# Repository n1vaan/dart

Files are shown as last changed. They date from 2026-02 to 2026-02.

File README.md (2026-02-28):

# DART - A custom 12-DOF Quadruped Robot
This is a smart quadruped robot dog that imitates the Boston Dynamics robot Spot. It uses inverse kinematics logic, along with visual input through cameras and quantitive measurements through an IMU to inform it's walking and movement algorithmns.

### Why we made it

We set out to build a quadruped robot to better understand how complex systems like locomotion, balance, and perception work together in robotics. This project gave us the opportunity to apply concepts like inverse kinematics, sensor integration, and real-time control in a hands-on way. Building a walking robot also pushed us to think carefully about both mechanical design and software logic.

## Fully Assembled Prototype 
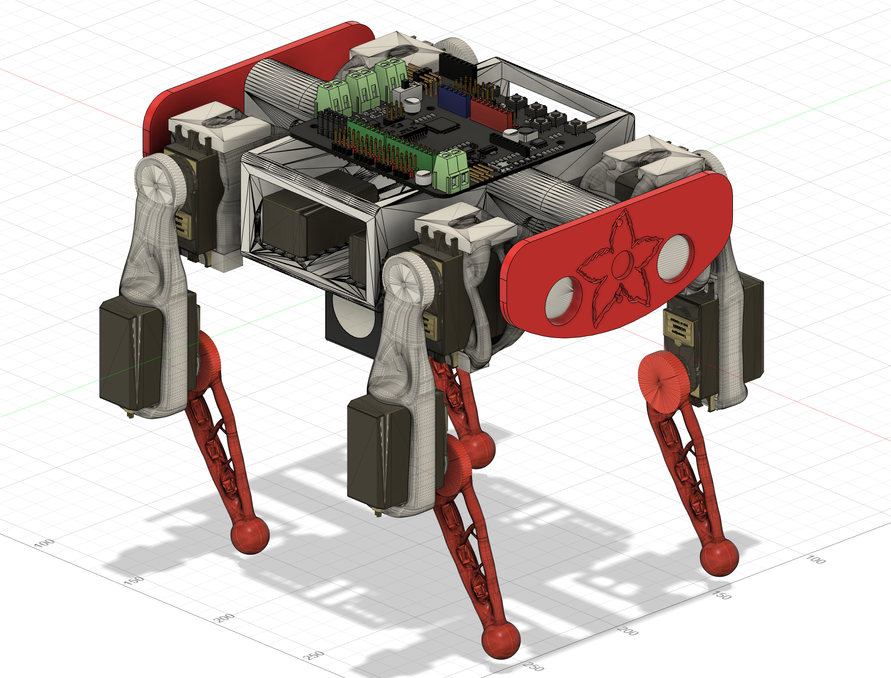
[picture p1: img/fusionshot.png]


## Rendered Prototype 
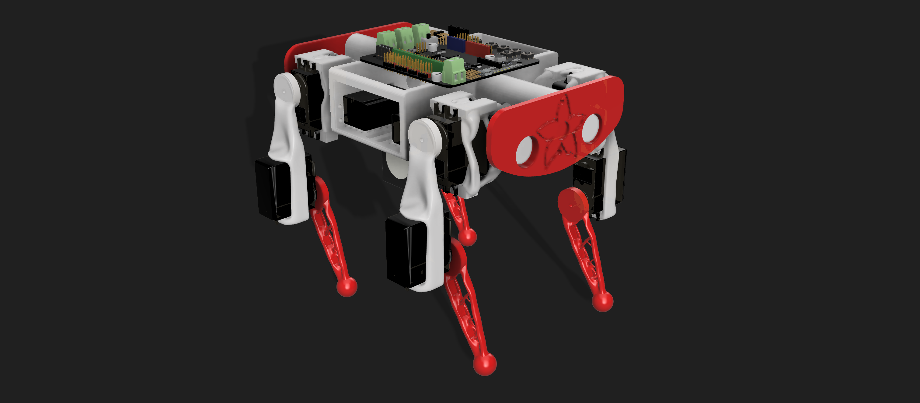
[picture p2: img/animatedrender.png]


## Circuit 
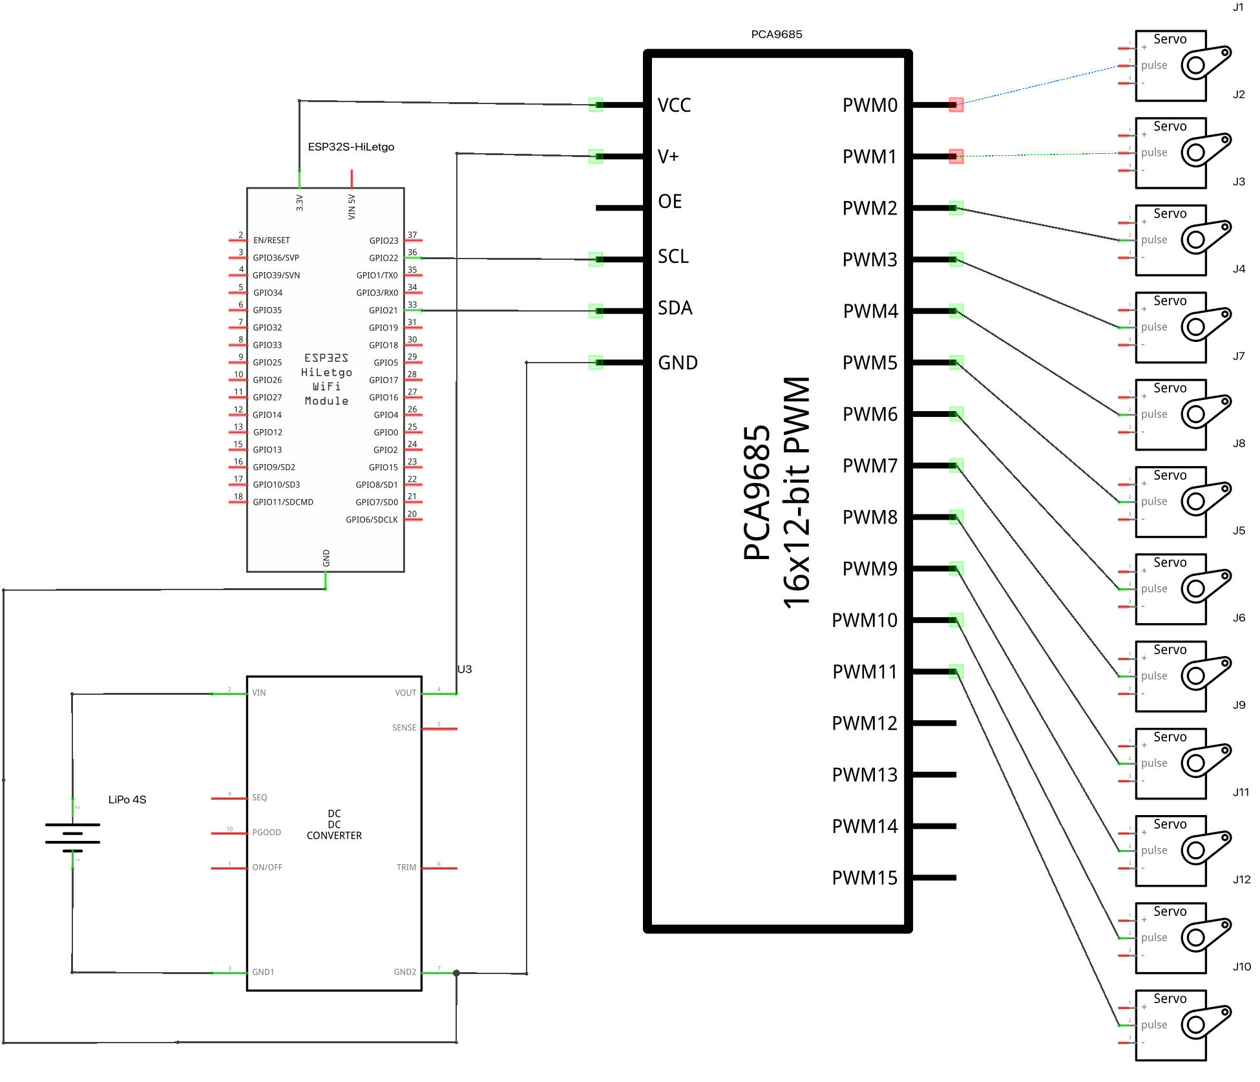
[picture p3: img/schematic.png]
Circuitry

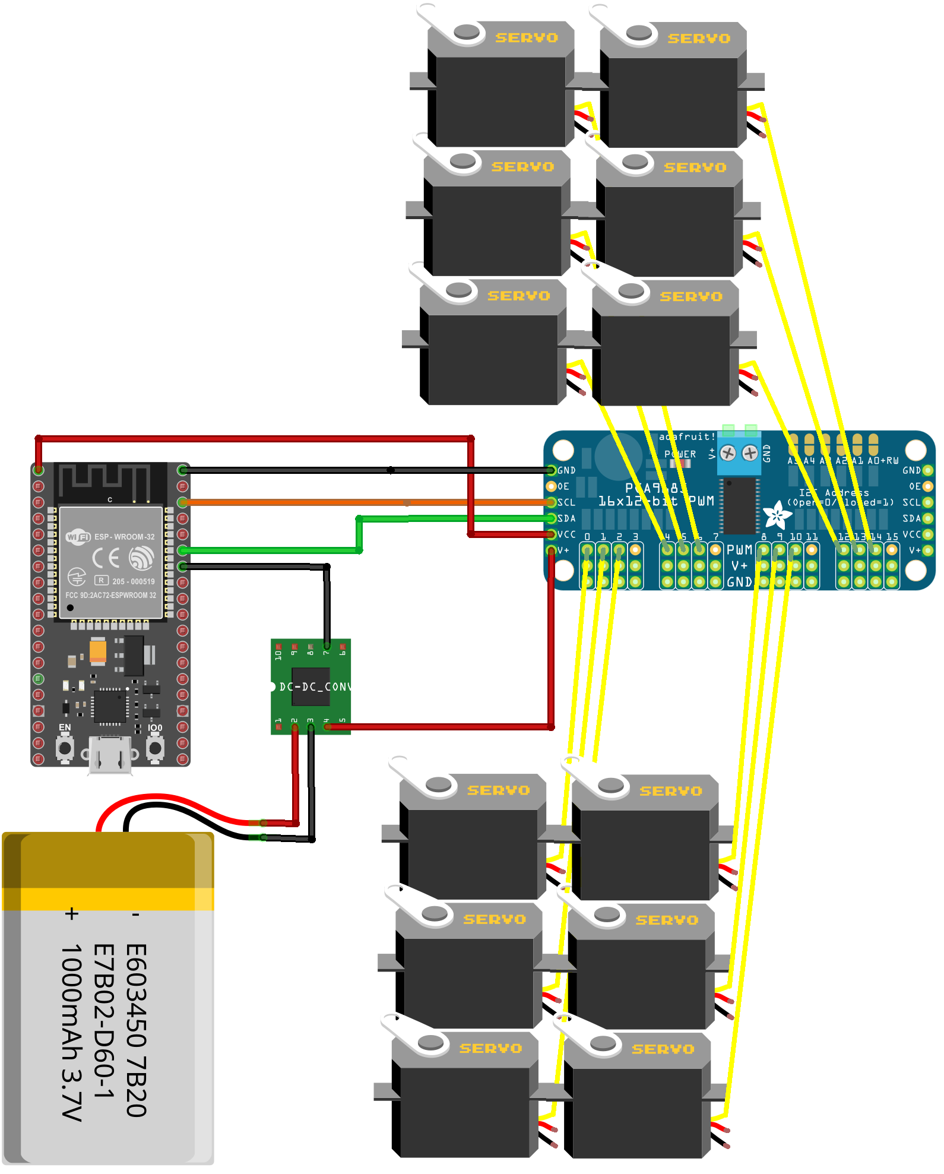
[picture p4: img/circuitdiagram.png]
Diagram


## Bill of Materials (BOM)

| Component | Quantity | Price Estimate | Link |
|---|---|---|---|
| 12 AWG Silicone Wire (Red/Black) | 1 | $11.64 | https://www.aliexpress.us/item/3256808377087848.html |
| 30A 2×12 Position Terminal Block Distribution Module | 1 | $9.63 | https://www.aliexpress.us/item/3256805810671782.html |
| LM2596S Adjustable Buck Converter (5V Logic Rail) | 1 | $8.43 | https://www.aliexpress.us/item/3256808555816134.html |
| 300W 20A DC-DC Adjustable Buck Converter (Servo Rail) | 1 | $3.83 | https://www.aliexpress.us/item/3256805882203198.html |
| 12 AWG Inline Fuse Holder | 1 | $4.91 | https://www.aliexpress.us/item/3256809222471794.html |
| 4700µF 25V Electrolytic Capacitors (10pcs) | 1 | $2.23 | https://www.aliexpress.us/item/3256806684037967.html |
| Heat Shrink Tubing Kit | 1 | $0.99 | https://www.aliexpress.us/item/3256808709374117.html |
| PCA9685 16-Channel PWM Driver Board | 1 | $3.73 | https://www.aliexpress.us/item/3256810242626835.html |
| 22 AWG Servo Extension Cables (20 Pack) | 1 | $1.59 | https://www.aliexpress.us/item/3256807778609444.html |
| 2S 5200mAh 80C LiPo Battery | 1 | $26.16 | https://www.aliexpress.us/item/3256811494310839.html |
| Miuzei 20KG Digital Servos (4 Pack ×3 = 12 Servos) | 3 | $134.97 | https://www.amazon.com/dp/B0FH53CKCS |
| **Total (Estimated)** | — | **$208.11** | — |

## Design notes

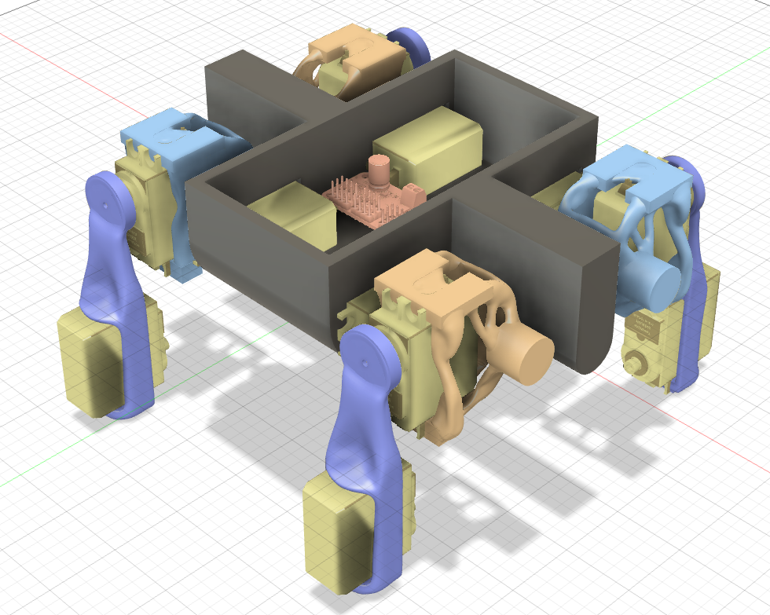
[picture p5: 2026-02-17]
img/day3.png

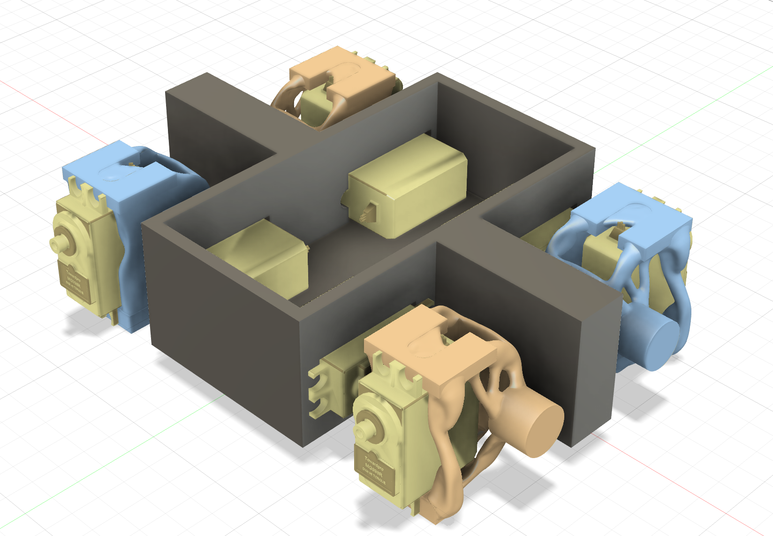
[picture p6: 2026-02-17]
img/day2_4.png

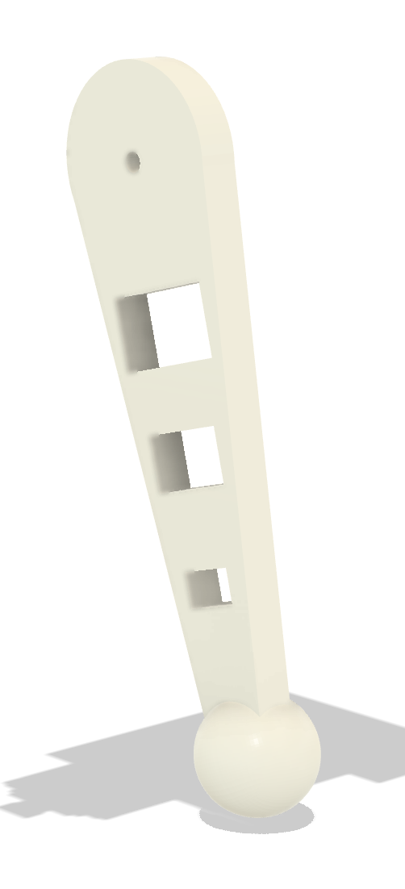
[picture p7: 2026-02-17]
img/last_joint.png

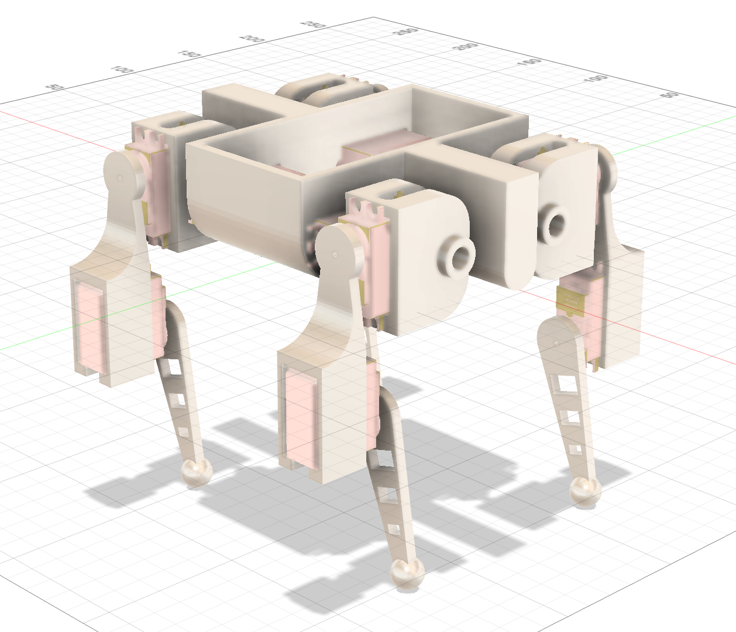
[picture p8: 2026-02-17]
img/newproto.png

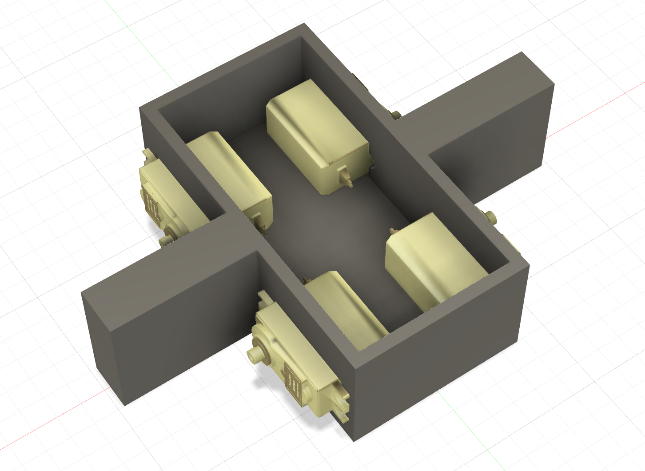
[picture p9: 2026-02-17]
img/day1.png

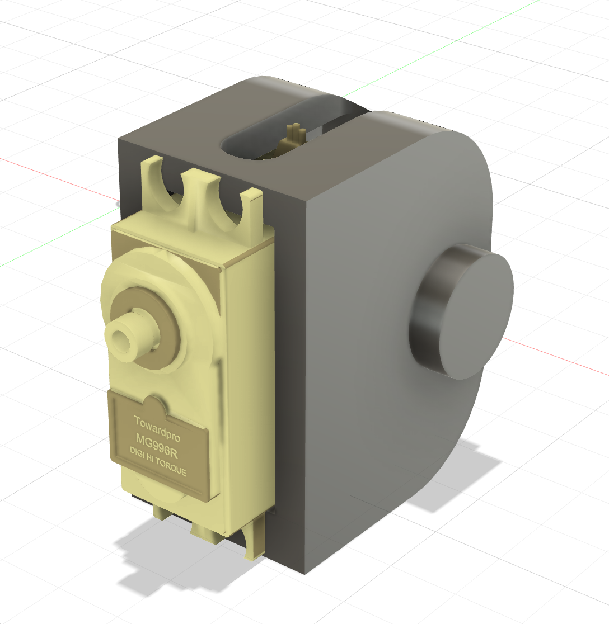
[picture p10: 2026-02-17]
img/day2.png

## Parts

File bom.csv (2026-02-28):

Item | Quantity | Unit Price (USD) | Total (USD) | Link
Miuzei 20KG Digital Servos (4 Pack) | 3 | 44.99 | 134.97 | https://www.amazon.com/dp/B0FH53CKCS
12 AWG Silicone Wire (Red/Black) | 1 | 11.64 | 11.64 | https://www.aliexpress.us/item/3256808377087848.html
30A 2x12 Terminal Block Distribution Module | 1 | 9.63 | 9.63 | https://www.aliexpress.us/item/3256805810671782.html
LM2596S Adjustable Buck Converter (5V Logic Rail) | 1 | 8.43 | 8.43 | https://www.aliexpress.us/item/3256808555816134.html
300W 20A DC-DC Buck Converter (Servo Rail) | 1 | 3.83 | 3.83 | https://www.aliexpress.us/item/3256805882203198.html
Inline Fuse Holders | 1 | 4.91 | 4.91 | https://www.aliexpress.us/item/3256809222471794.html
4700µF 25V Electrolytic Capacitors (10pcs) | 1 | 2.23 | 2.23 | https://www.aliexpress.us/item/3256806684037967.html
Heat Shrink Tubing Kit | 1 | 0.99 | 0.99 | https://www.aliexpress.us/item/3256808709374117.html
PCA9685 16-Channel PWM Driver Board | 1 | 3.73 | 3.73 | https://www.aliexpress.us/item/3256810242626835.html
22 AWG Servo Extension Cables (10 Pack) | 2 | 1.59 | 1.59 | https://www.aliexpress.us/item/3256807778609444.html
2S 5200mAh 80C LiPo Battery | 1 | 26.16 | 26.16 | https://www.aliexpress.us/item/3256811494310839.html
Total |  |  | 208.11

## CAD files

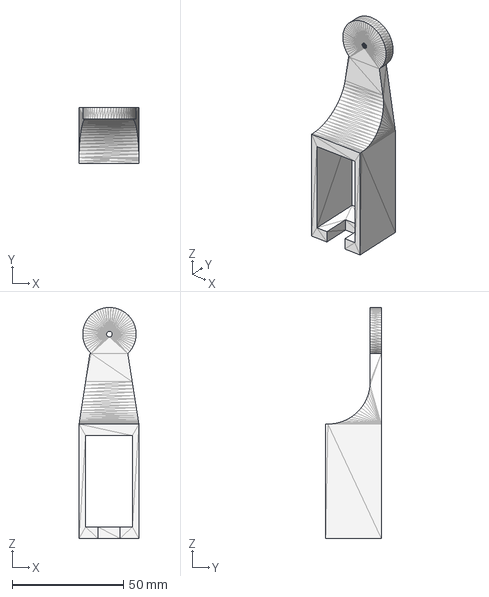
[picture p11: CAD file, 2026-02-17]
cad/stepindividual/KneeBraceNew.step
26.9 x 25.0 x 103.8 mm

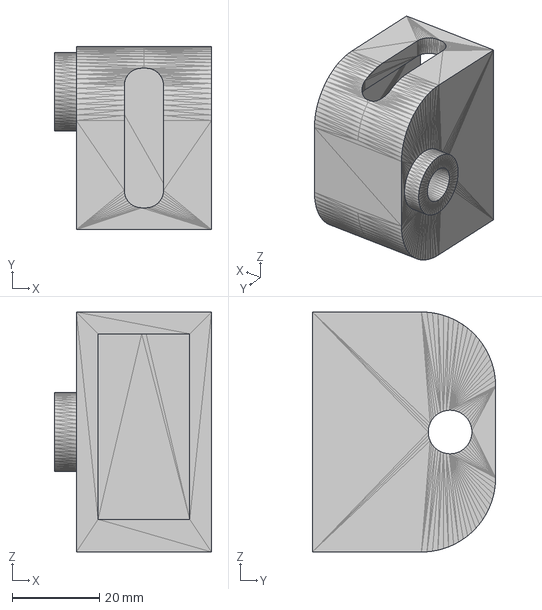
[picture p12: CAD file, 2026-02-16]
cad/stepindividual/HipBraceNew2.step
36.0 x 42.0 x 55.0 mm

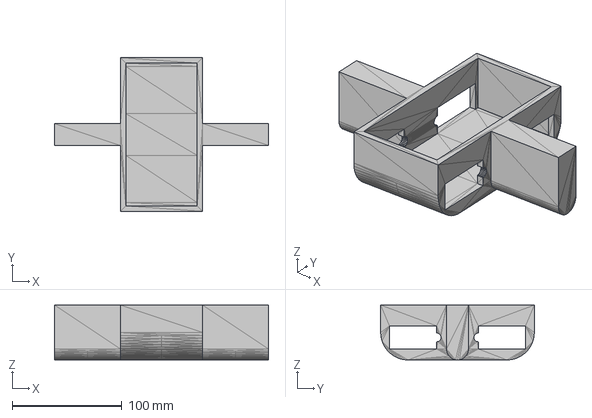
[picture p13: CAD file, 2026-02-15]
cad/stepindividual/CenterNew.step
195.0 x 140.0 x 50.0 mm

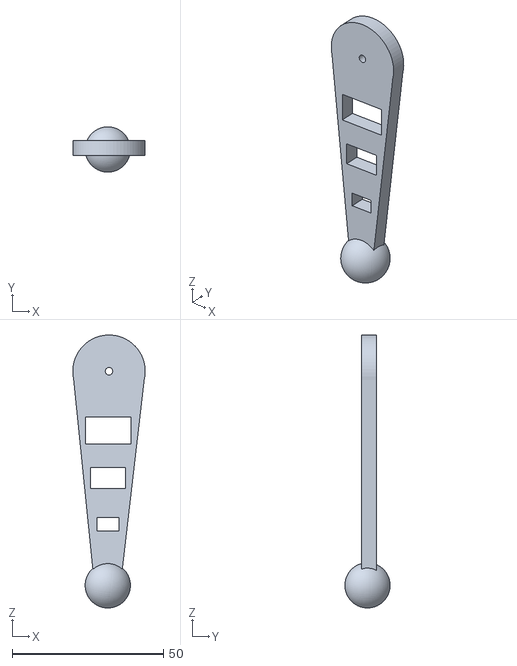
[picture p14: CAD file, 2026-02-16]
cad/stl/FinalLimbNew.stl
24.0 x 15.0 x 90.4

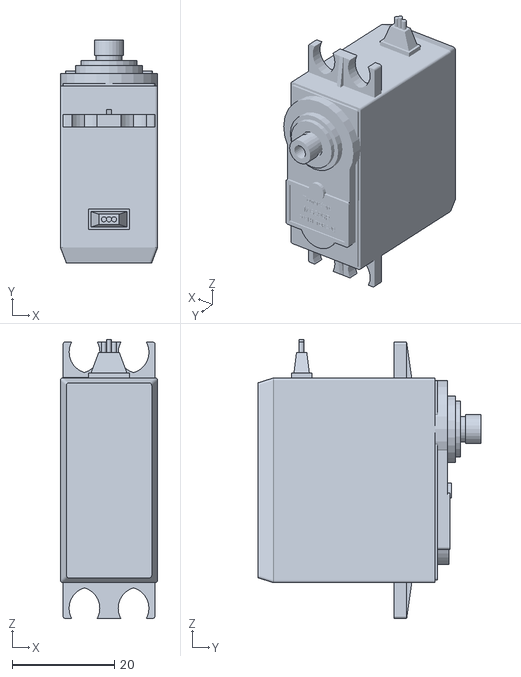
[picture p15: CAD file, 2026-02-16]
cad/stl/MG996RServo.stl
19.0 x 43.5 x 54.5

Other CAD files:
cad/stl/KneeBraceNew.stl
cad/stl/HipBraceNew2.stl
cad/stepindividual/HipBraceNew1.step
cad/stl/HipBraceNew1.stl
cad/stl/CenterNew.stl

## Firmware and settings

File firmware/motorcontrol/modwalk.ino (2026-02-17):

#include <Servo.h>
#include <Wire.h>
#include <Adafruit_Sensor.h>
#include <Adafruit_BNO055.h>
#include <utility/imumaths.h>
#include <math.h>

Adafruit_BNO055 bno = Adafruit_BNO055(55);

Servo backHipRight;
Servo frontHipRight;
Servo frontHipLeft;
Servo backHipLeft;

const int L1 = 75; 
const int L2 = 80;

Servo backArmLeft;
Servo backArmRight;
Servo frontArmRight;
Servo frontArmLeft;

Servo frontKneeRight;
Servo frontKneeLeft;
Servo backKneeLeft;
Servo backKneeRight;

struct ServoMap {
  const char* name;
  int angle;        
};

ServoMap config[] = {
  {"backHipRight", 90},
  {"frontHipRight", 95},
  {"frontHipLeft", 100},
  {"backHipLeft", 80},
  {"backArmLeft", 100},
  {"backArmRight", 90},
  {"frontArmRight", 50},
  {"frontArmLeft", 90},
  {"frontKneeRight", 90},
  {"frontKneeLeft", 90},
  {"backKneeLeft", 15},
  {"backKneeRight", 90}
};

const int NUM_SERVOS = sizeof(config)/sizeof(config[0]);

int currentAngle[NUM_SERVOS];

const int pinBackHipRight = 2;
const int pinFrontHipRight = 3; 
const int pinFrontHipLeft = 4; 
const int pinBackHipLeft = 5;

const int pinBackArmLeft = 6;
const int pinBackArmRight = 7;
const int pinFrontArmRight = 8;
const int pinFrontArmLeft = 9;

const int pinFrontKneeRight = 10;
const int pinFrontKneeLeft = 11;
const int pinBackKneeLeft = 12;
const int pinBackKneeRight = 13;

bool setServoAngle(String name, int angle);
void applyConfig();


int getCurrentAngle(const char* name) {
  for (int i = 0; i < NUM_SERVOS; i++) {
    if (strcmp(config[i].name, name) == 0) {
      return currentAngle[i];
    }
  }
  return 90;
}

bool setServoAngle(String name, int angle) {

  // Move servo
  if      (name == "backHipRight")  backHipRight.write(angle);
  else if (name == "frontHipRight") frontHipRight.write(angle);
  else if (name == "frontHipLeft")  frontHipLeft.write(angle);
  else if (name == "backHipLeft")   backHipLeft.write(angle);
  else if (name == "backArmLeft")   backArmLeft.write(angle);
  else if (name == "backArmRight")  backArmRight.write(angle);
  else if (name == "frontArmRight") frontArmRight.write(angle);
  else if (name == "frontArmLeft")  frontArmLeft.write(angle);
  else if (name == "frontKneeRight") frontKneeRight.write(angle);
  else if (name == "frontKneeLeft")  frontKneeLeft.write(angle);
  else if (name == "backKneeLeft")   backKneeLeft.write(angle);
  else if (name == "backKneeRight")  backKneeRight.write(angle);
  else return false;

  for (int i = 0; i < NUM_SERVOS; i++) {
    if (strcmp(config[i].name, name.c_str()) == 0) {
      currentAngle[i] = angle;
      break;
    }
  }

  return true;
}

void applyConfig() {
  for (int i = 0; i < NUM_SERVOS; i++) {
    setServoAngle(config[i].name, config[i].angle);
  }
}

int getConfigAngle(const char* name) {
  for (int i = 0; i < NUM_SERVOS; i++) {
    if (strcmp(config[i].name, name) == 0) {
      return config[i].angle;
    }
  }
  return 90;  
}

void setGradualServo(String servo, int current, int angle, int delayTime, int offset) {
  int diff = angle - current;
  int stepDir = (diff >= 0) ? 1 : -1;
  int steps = abs(diff) / offset;

  for (int i = 0; i <= steps; i++) {
    int newAngle = current + stepDir * i * offset;
    setServoAngle(servo, newAngle);
    delay(delayTime);
  }

  setServoAngle(servo, angle);
}

void shiftCOM(String legName, int offset, int delayTime = 5) {

  if (legName == "frontLeft") {
    setGradualServo("frontHipLeft",  getCurrentAngle("frontHipLeft"),  getCurrentAngle("frontHipLeft")  + offset/2, delayTime, 1);
    setGradualServo("frontArmLeft",  getCurrentAngle("frontArmLeft"),  getCurrentAngle("frontArmLeft")  + offset/2, delayTime, 1);
    setGradualServo("frontKneeLeft",  getCurrentAngle("frontKneeLeft"),  getCurrentAngle("frontKneeLeft")  + offset/2, delayTime, 1);
  }

  else if (legName == "frontRight") {
    setGradualServo("frontHipRight", getCurrentAngle("frontHipRight"), getCurrentAngle("frontHipRight") - offset, delayTime, 1);
    setGradualServo("frontArmRight",  getCurrentAngle("frontArmRight"),  getCurrentAngle("frontArmRight")  + offset/2, delayTime, 1);
    setGradualServo("frontKneeRight",  getCurrentAngle("frontKneeRight"),  getCurrentAngle("frontKneeRight")  - offset/2, delayTime, 1);


  }

  else if (legName == "backLeft") {
    setGradualServo("backHipLeft",   getCurrentAngle("backHipLeft"),   getCurrentAngle("backHipLeft")   - offset, delayTime, 1);
    setGradualServo("backArmLeft",   getCurrentAngle("backArmLeft"),   getCurrentAngle("backArmLeft")   + offset, delayTime, 1);
    setGradualServo("backKneeLeft",   getCurrentAngle("backKneeLeft"),   getCurrentAngle("backKneeLeft")   + offset, delayTime, 1);
  }

  else if (legName == "backRight") {
    setGradualServo("backHipRight",  getCurrentAngle("backHipRight"),  getCurrentAngle("backHipRight")  + offset, delayTime, 1);
    setGradualServo("backArmRight",   getCurrentAngle("backArmRight"),   getCurrentAngle("backArmRight")   - offset, delayTime, 1);
    setGradualServo("backKneeRight",   getCurrentAngle("backKneeRight"),   getCurrentAngle("backKneeRight")   - offset, delayTime, 1);

  }
}

void walkForward(int steps, int delayTime, int dxFrontKnee, int dxBackKnee, int dxFrontArm, int dxBackArm) {
  for (int i = 0; i < steps; i++) {

    shiftCOM("backRight", 10);
    setServoAngle("frontKneeLeft", getCurrentAngle("frontKneeLeft") + dxFrontKnee);
    delay(delayTime);
    setServoAngle("frontArmLeft", getCurrentAngle("frontArmLeft") - dxFrontArm);
    delay(delayTime);
    shiftCOM("backRight", -10);

    shiftCOM("frontLeft", 5);
    setServoAngle("backKneeRight", getCurrentAngle("backKneeRight") - dxBackKnee);
    delay(delayTime);
    setServoAngle("backArmRight", getCurrentAngle("backArmRight") + dxBackArm);
    delay(delayTime);
    shiftCOM("frontLeft", -5);

    setServoAngle("frontKneeLeft", getConfigAngle("frontKneeLeft"));
    delay(delayTime);
    setServoAngle("frontArmLeft", getConfigAngle("frontArmLeft"));
    delay(delayTime);
    setServoAngle("backKneeRight", getConfigAngle("backKneeRight"));
    delay(delayTime);
    setServoAngle("backArmRight", getConfigAngle("backArmRight"));
    delay(delayTime);


    shiftCOM("backLeft", 15);
    setServoAngle("frontKneeRight", getCurrentAngle("frontKneeRight") - dxFrontKnee);
    delay(delayTime);
    setServoAngle("frontArmRight", getCurrentAngle("frontArmRight") + dxFrontArm);
    delay(delayTime);
    shiftCOM("backLeft", -15);

    shiftCOM("frontRight", 5);
    setServoAngle("backKneeLeft", getCurrentAngle("backKneeLeft") + dxBackKnee);
    delay(delayTime);
    setServoAngle("backArmLeft", getCurrentAngle("backArmLeft") - dxBackArm);
    delay(delayTime);
    shiftCOM("frontRight", -5);

    setServoAngle("frontKneeRight", getConfigAngle("frontKneeRight"));
    delay(delayTime);
    setServoAngle("frontArmRight", getConfigAngle("frontArmRight"));
    delay(delayTime);
    setServoAngle("backKneeLeft", getConfigAngle("backKneeLeft"));
    delay(delayTime);
    setServoAngle("backArmLeft", getConfigAngle("backArmLeft"));
    delay(delayTime);

    delay(delayTime * 2);
  }
}

void setup() {
  Serial.begin(9600);  
  while(!Serial);

  backHipRight.attach(pinBackHipRight);
  frontHipRight.attach(pinFrontHipRight);
  frontHipLeft.attach(pinFrontHipLeft);
  backHipLeft.attach(pinBackHipLeft);

  backArmLeft.attach(pinBackArmLeft);
  backArmRight.attach(pinBackArmRight);
  frontArmRight.attach(pinFrontArmRight);
  frontArmLeft.attach(pinFrontArmLeft);

  frontKneeRight.attach(pinFrontKneeRight);
  frontKneeLeft.attach(pinFrontKneeLeft);
  backKneeLeft.attach(pinBackKneeLeft);
  backKneeRight.attach(pinBackKneeRight);

  applyConfig();

  for (int i = 0; i < NUM_SERVOS; i++) {
    currentAngle[i] = config[i].angle;
  }

}

void handleSerial(String cmd) {
  Serial.println("CMD: " + cmd);

  if (cmd.startsWith("set ")) {
    cmd.remove(0, 4);
    int spaceIndex = cmd.indexOf(' ');
    if (spaceIndex == -1) {
      Serial.println("ERR: invalid set format");
      return;
    }
    String servo = cmd.substring(0, spaceIndex);
    int angle = cmd.substring(spaceIndex + 1).toInt();

    if (setServoAngle(servo, angle)) {
      Serial.println("OK SET " + servo + " = " + String(angle));
    } else {
      Serial.println("ERR: servo not found");
    }
  }

  else if (cmd.startsWith("get ")) {
    cmd.remove(0, 4);
    int angle = getCurrentAngle(cmd.c_str());
    Serial.println("ANGLE " + cmd + " = " + String(angle));
  }

  else if (cmd.startsWith("walk ")) {
    int steps = cmd.substring(5).toInt();
    walkForward(steps, 200, 10, 10, 20, 10);
    Serial.println("OK WALK " + String(steps));
  }

  else if (cmd == "reset") {
    applyConfig();
    Serial.println("OK RESET");
  }

  else if (cmd.startsWith("shift ")) {
    cmd.remove(0, 6); // remove "shift "
    int spaceIndex = cmd.indexOf(' ');
    if (spaceIndex == -1) {
      Serial.println("ERR: invalid shift format");
      return;
    }

    String leg = cmd.substring(0, spaceIndex);
    int offset = cmd.substring(spaceIndex + 1).toInt();

    shiftCOM(leg, offset);
    Serial.println("OK SHIFT " + leg + " by " + String(offset));
  }

  else if (cmd == "list") {
    for (int i = 0; i < NUM_SERVOS; i++) {
      Serial.println(String(config[i].name) + " = " + String(currentAngle[i]));
    }
  }

  else {
    Serial.println("ERR: unknown command");
  }

}

void loop() {
  if (Serial.available()) {
    String command = Serial.readStringUntil('\n');
    command.trim();
    handleSerial(command);
  } 
}

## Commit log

2026-02-15 Added CAD
    [CenterNew.step, CenterNew.stl]
2026-02-17 Updated CAD
    [CenterNew.step, HipBraceNew1.step, HipBraceNew2.step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]
2026-02-17 Full Assemblies
2026-02-17 Add Bill of Materials section to README
    Added a Bill of Materials (BOM) section with components, quantities, price estimates, and links.
2026-02-17 Create bom.csv with components and pricing
    Added a bill of materials (BOM) with components, quantities, and price estimates.
    [bom.csv]
2026-02-28 Update BOM with new components and prices
2026-02-28 Modify BOM with new items and updated totals
    Updated quantities and prices for components in BOM.
    [bom.csv]
2026-02-28 Update LiPo battery details and total cost in README
